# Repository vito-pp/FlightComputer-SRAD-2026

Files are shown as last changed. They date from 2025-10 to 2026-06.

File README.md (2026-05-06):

# FlightComputer-SRAD-2026

---

# RP2040 Firmware Build Instructions

This project uses the Raspberry Pi Pico SDK with CMake and the ARM GCC toolchain.

Follow these steps to set up the build environment.

---

## 1. Install dependencies (Linux)

On Debian/Ubuntu:

```bash
sudo apt update
sudo apt install cmake gcc-arm-none-eabi libnewlib-arm-none-eabi build-essential git
```

On Fedora:

```bash
sudo dnf install cmake arm-none-eabi-gcc-cs arm-none-eabi-newlib make git
```

Check installation:

```bash
arm-none-eabi-gcc --version
cmake --version
```

---

## 2. Download the Pico SDK

Clone the SDK somewhere on your system (outside this repo):

```bash
git clone https://github.com/raspberrypi/pico-sdk.git ~/pico-sdk
```

---

## 3. Set the SDK path environment variable

Set this variable so CMake can find the SDK:

```bash
export PICO_SDK_PATH=~/pico-sdk
```

To make it permanent (bash):

```bash
echo 'export PICO_SDK_PATH=~/pico-sdk' >> ~/.bashrc
source ~/.bashrc
```

---

## 4. Build the project

From the `code/` directory:

```bash
mkdir build
cd build
cmake ..
make -j$(nproc)
```

After building, the firmware file will be generated:

```bash
flight_computer.uf2
```

---

## 5. Flash to the RP2040

1. Hold the **BOOTSEL** button on the Pico
2. Plug the Pico into USB
3. Release BOOTSEL
4. Copy the UF2 file:

```bash
cp flight_computer.uf2 /media/$USER/RPI-RP2/
```

(The mount path may vary depending on your system.)

---

## 6. Rebuilding later

After the first build, you usually only need:

```bash
cd code/build
make -j$(nproc)
```

If you change `CMakeLists.txt`, run:

```bash
cmake ..
```

If something breaks, clean build:

```bash
cd code
rm -rf build
mkdir build
cd build
cmake ..
make -j$(nproc)
```

## Submodules / External Libraries

This project uses the SD-card library `no-OS-FatFS-SD-SDIO-SPI-RPi-Pico` as a Git submodule.

### Fresh clone

Clone with submodules:

```bash
git clone --recurse-submodules <repo-url>
```

### Existing clone

If the repository was already cloned without submodules:

```bash
git submodule update --init --recursive
```

After pulling updates:

```bash
git pull --recurse-submodules
git submodule update --init --recursive
```

### SD-card library notes

This project uses:

```text
no-OS-FatFS-SD-SDIO-SPI-RPi-Pico
```

in SDIO/PIO 4-bit mode.

The library contains a project-specific patch because the SD clock pin is routed differently on this board.

SD pin mapping:

```text
SD_CMD  -> GPIO18
SD_DAT0 -> GPIO19
SD_DAT1 -> GPIO20
SD_DAT2 -> GPIO21
SD_DAT3 -> GPIO22
SD_CLK  -> GPIO25
```

The SDIO PIO configuration was modified with:

```text
SDIO_CLK_PIN_D0_OFFSET = 6
```

The patched submodule commit must be available from the configured submodule remote.

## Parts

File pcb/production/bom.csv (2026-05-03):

Designator | Footprint | Quantity | Value | LCSC Part #
A1 | XDCR_MS561101BA03-50 | 1 | MS561101BA03-50
AE1 | XDCR_W3011 | 1 | W3011
C10, C8 | 0402 | 2 | 1u
C11, C12, C13, C14, C15, C16, C6, C7, C9, CADXL_1, CBAR_1, CBAR_2, CFLASH_1, CIIM_1, CIIM_2, CIIM_3, CIIM_4 | 0402 | 17 | 100n
CADXL_2, CGPS_1, CXB_2 | 0805 | 3 | 1u
CGPS_2 | 0603 | 1 | 100n
CPS_1, CPS_2, CPS_3 | 0805 | 3 | 10u
CXB_1 | 0805 | 1 | 47p
CX_1, CX_2 | 0805 | 2 | 15p
D1 | 0603 | 1 | LED_B
D2 | 0603 | 1 | LED_R
DIV_RES_REG1A1, DIV_RES_REG2A1 | 0805 | 2 | 82k
DIV_RES_REG1B1 | 0805 | 1 | 150k
DIV_RES_REG2B1 | 0805 | 1 | 47k
J1 | MOLEX_503398-1892 | 1 | 503398-1892
J2 | PinHeader_1x03_P2.54mm_Vertical | 1 | Connector_3
J3 | USB_Micro-B_Amphenol_10103594-0001LF_Horizontal | 1 | USB_B_Micro
J5 | Molex_1x02_P2.54mm | 1 | Vin_Bat
LS1 | Buzzer_TDK_PS1240P02BT_D12.2mm_H6.5mm | 1 | PS1240P02BT
Q1 | SOT-23 | 1 | BC847
R1 | 0805 | 1 | 22k
R2, RFLASH_2, RX_1 | 0805 | 3 | 1k
R3, R4 | 0603 | 2 | 27
R6, R7, R_RST1 | 0805 | 3 | 10k
RI2C_1, RI2C_2, RI2C_3, RI2C_4 | 0603 | 4 | 1k
RL_1 | 0805 | 1 | 39
RL_2 | 0805 | 1 | 150
RSPI_4 | 0603 | 1 | 10k
S1, S2 | PTS810SJK250SMTRLFS | 2 | PTS810SJK250SMTR_LFS
TP1, TP2, TP3 | TestPoint_Pad_D1.0mm | 3 | TestPoint
U1 | QFN50P450X450X115-25N | 1 | IIM-20670
U3 | QFN-56-1EP_7x7mm_P0.4mm_EP3.2x3.2mm_ThermalVias | 1 | RP2040
U4 | LGA-14_3x5mm_P0.8mm_LayoutBorder1x6y | 1 | ADXL375BCCZ-RL7
U5 | XCVR_MAX-M10M-00B | 1 | MAX-M10M-00B
U6 | SOIC-8_5.3x5.3mm_P1.27mm | 1 | W25Q128JVS
U7 | XBEEPRO | 1 | XBP9B-DMSTB002
U8 | SOT-223-6 | 1 | TPS73733DCQ
Y1 | XTAL_ABM8-272-T3 | 1 | ABM8-272-T3

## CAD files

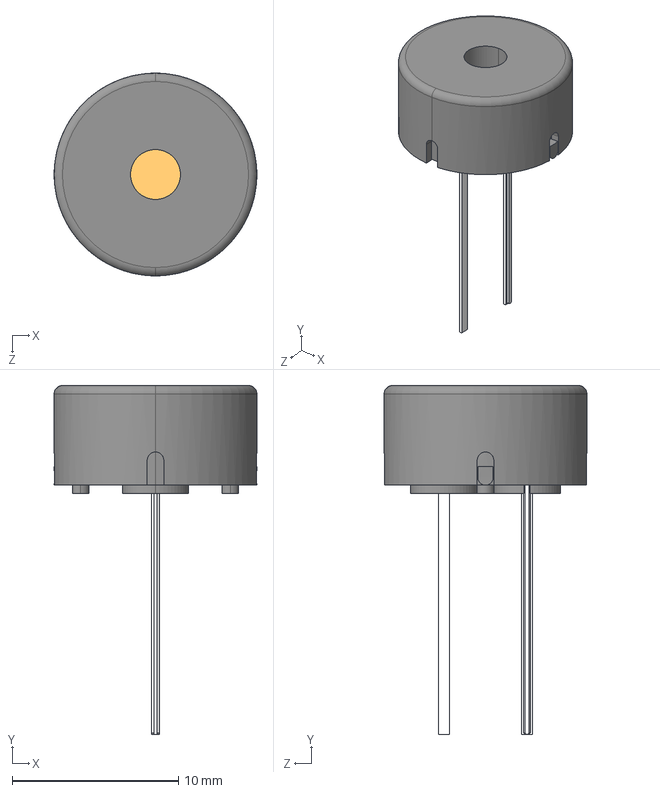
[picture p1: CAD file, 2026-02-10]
pcb/components/3d_models/PS1240P02BT.step
12.2 x 21.0 x 12.2 mm

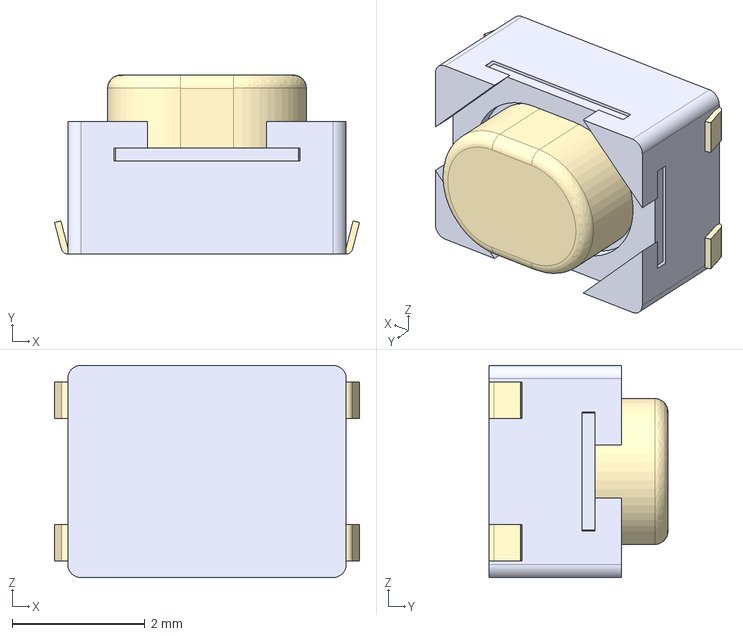
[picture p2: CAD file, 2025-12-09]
pcb/components/3d_models/PTS810SJK250SMTR_LFS.step
4.60 x 2.70 x 3.20 mm

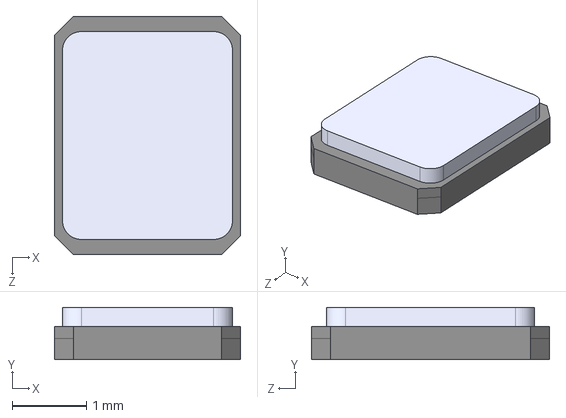
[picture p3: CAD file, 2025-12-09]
pcb/components/3d_models/ABM8-272-T3.STEP
2.50 x 0.7 x 3.20 mm

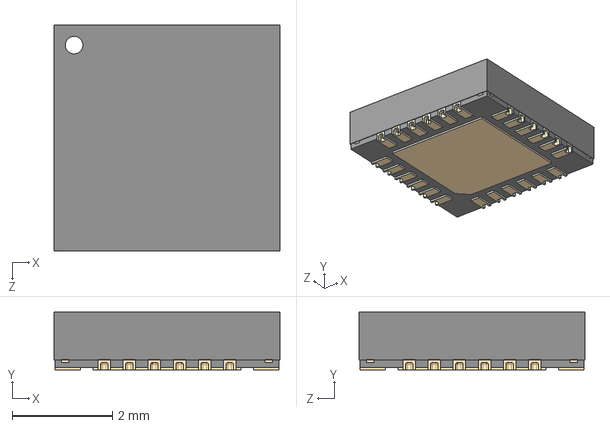
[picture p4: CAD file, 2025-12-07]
pcb/components/3d_models/IIM-20670--3DModel-STEP-269445.STEP
4.50 x 1.15 x 4.50 mm

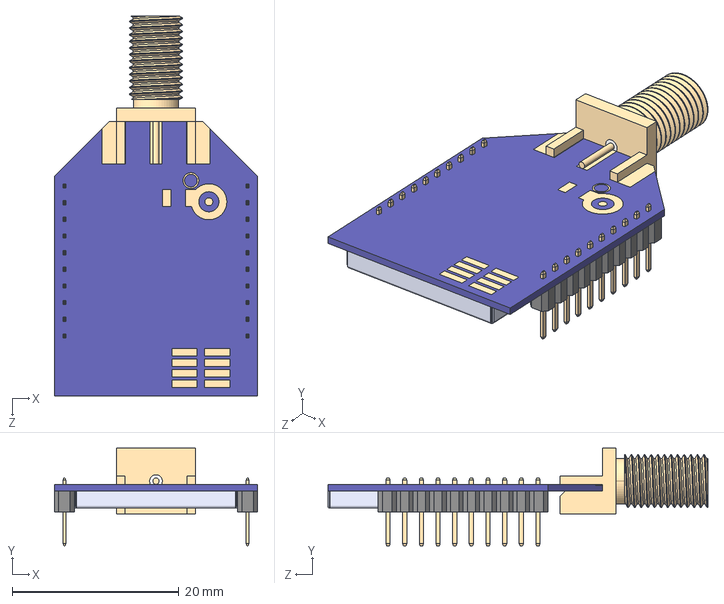
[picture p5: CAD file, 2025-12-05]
pcb/components/3d_models/XBP9B-DMSTB002.step
24.4 x 11.7 x 45.6 mm

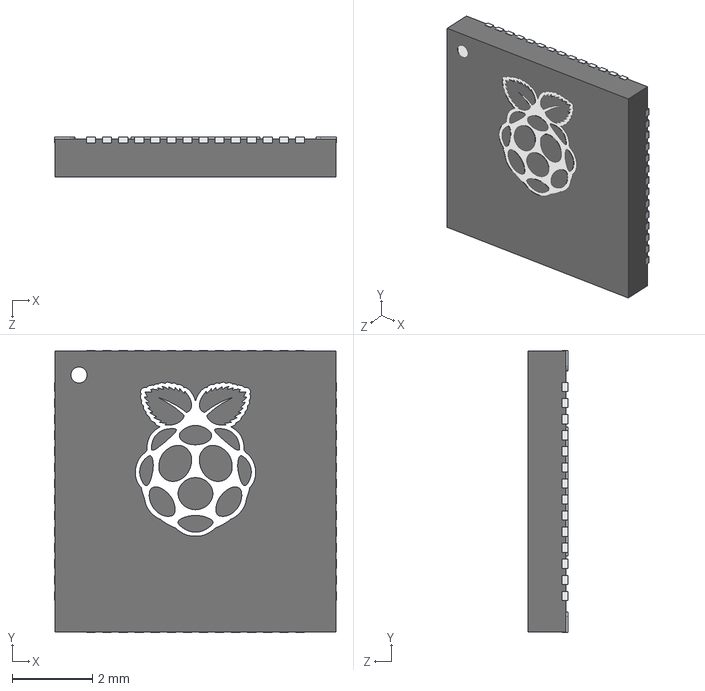
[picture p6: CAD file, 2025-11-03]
pcb/components/3d_models/RP2040_QFN_PACKAGE.STEP
7.02 x 7.02 x 1.00 mm

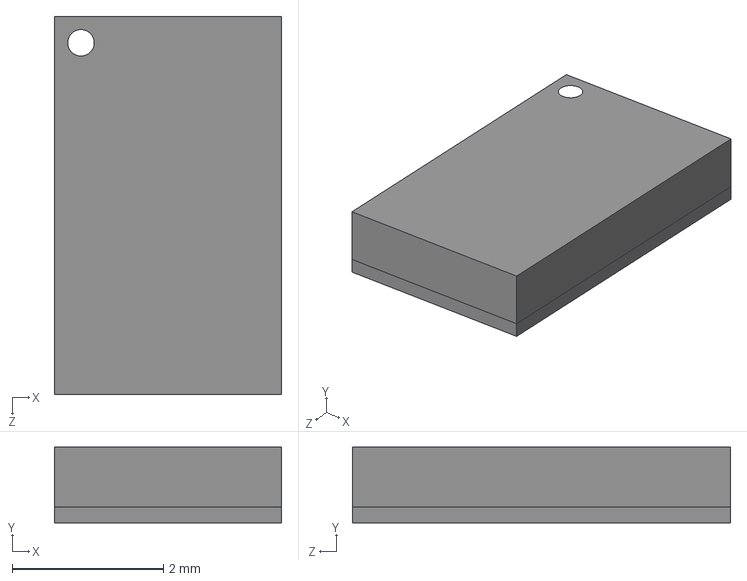
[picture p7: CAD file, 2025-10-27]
pcb/components/3d_models/ADXL375BCCZ-RL7.STEP
3.00 x 1.00 x 5.00 mm

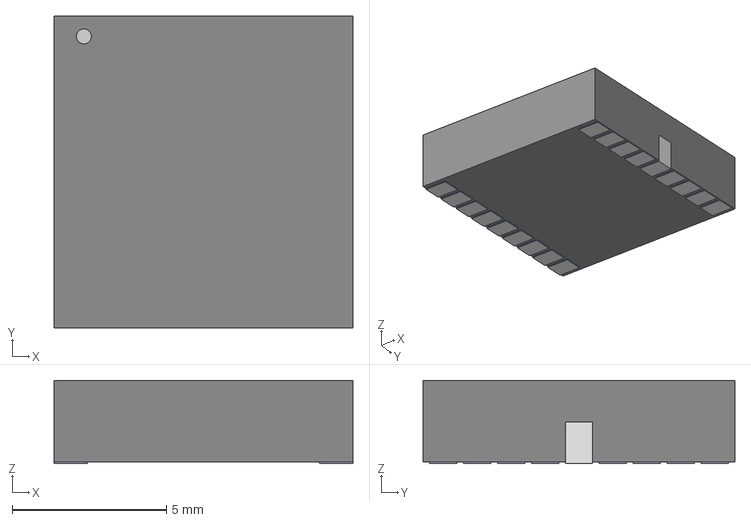
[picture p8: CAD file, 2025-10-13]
pcb/components/3d_models/MOD18_MAX-M10M_UBL.step
9.70 x 10.1 x 2.69 mm

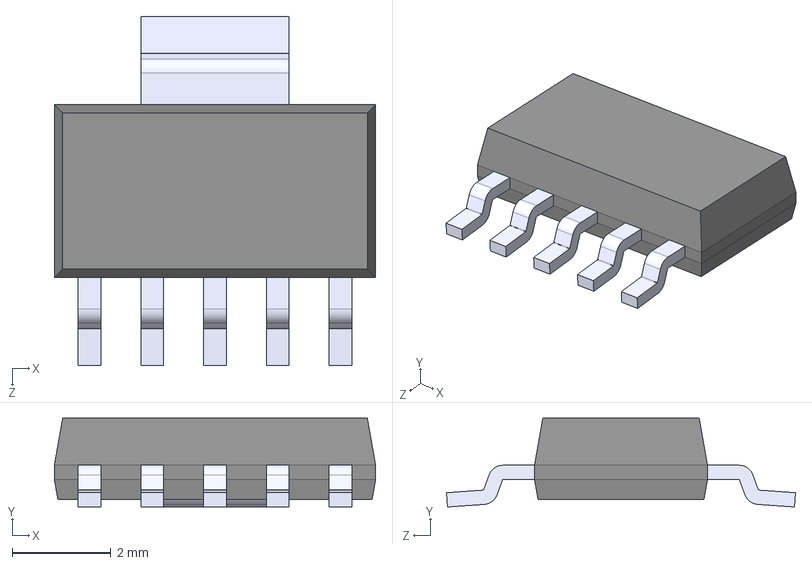
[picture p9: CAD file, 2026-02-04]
pcb/components/symbols/TPS73733DCQ.step
6.50 x 1.80 x 7.06 mm

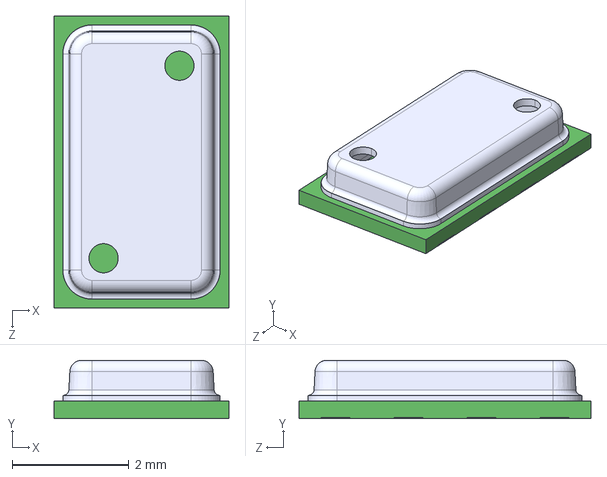
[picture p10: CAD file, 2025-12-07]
pcb/components/3d_models/MS561101BA03-50--3DModel-STEP-56544.STEP
3.00 x 1.00 x 5.00 mm

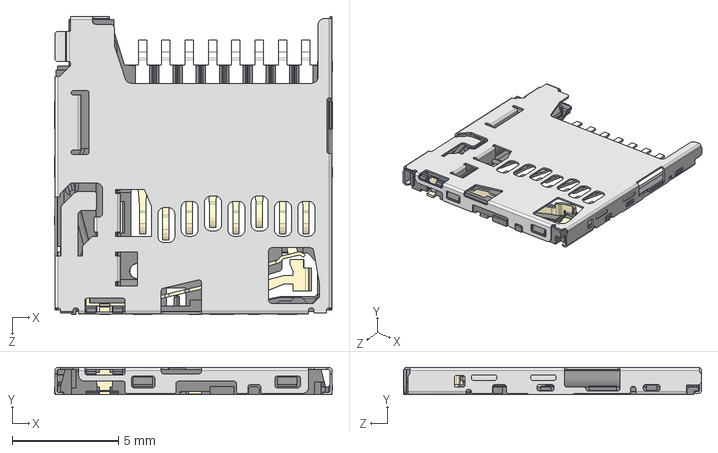
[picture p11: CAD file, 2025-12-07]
pcb/components/3d_models/503398-1892--3DModel-STEP-56544.STEP
13.1 x 1.28 x 14.1 mm

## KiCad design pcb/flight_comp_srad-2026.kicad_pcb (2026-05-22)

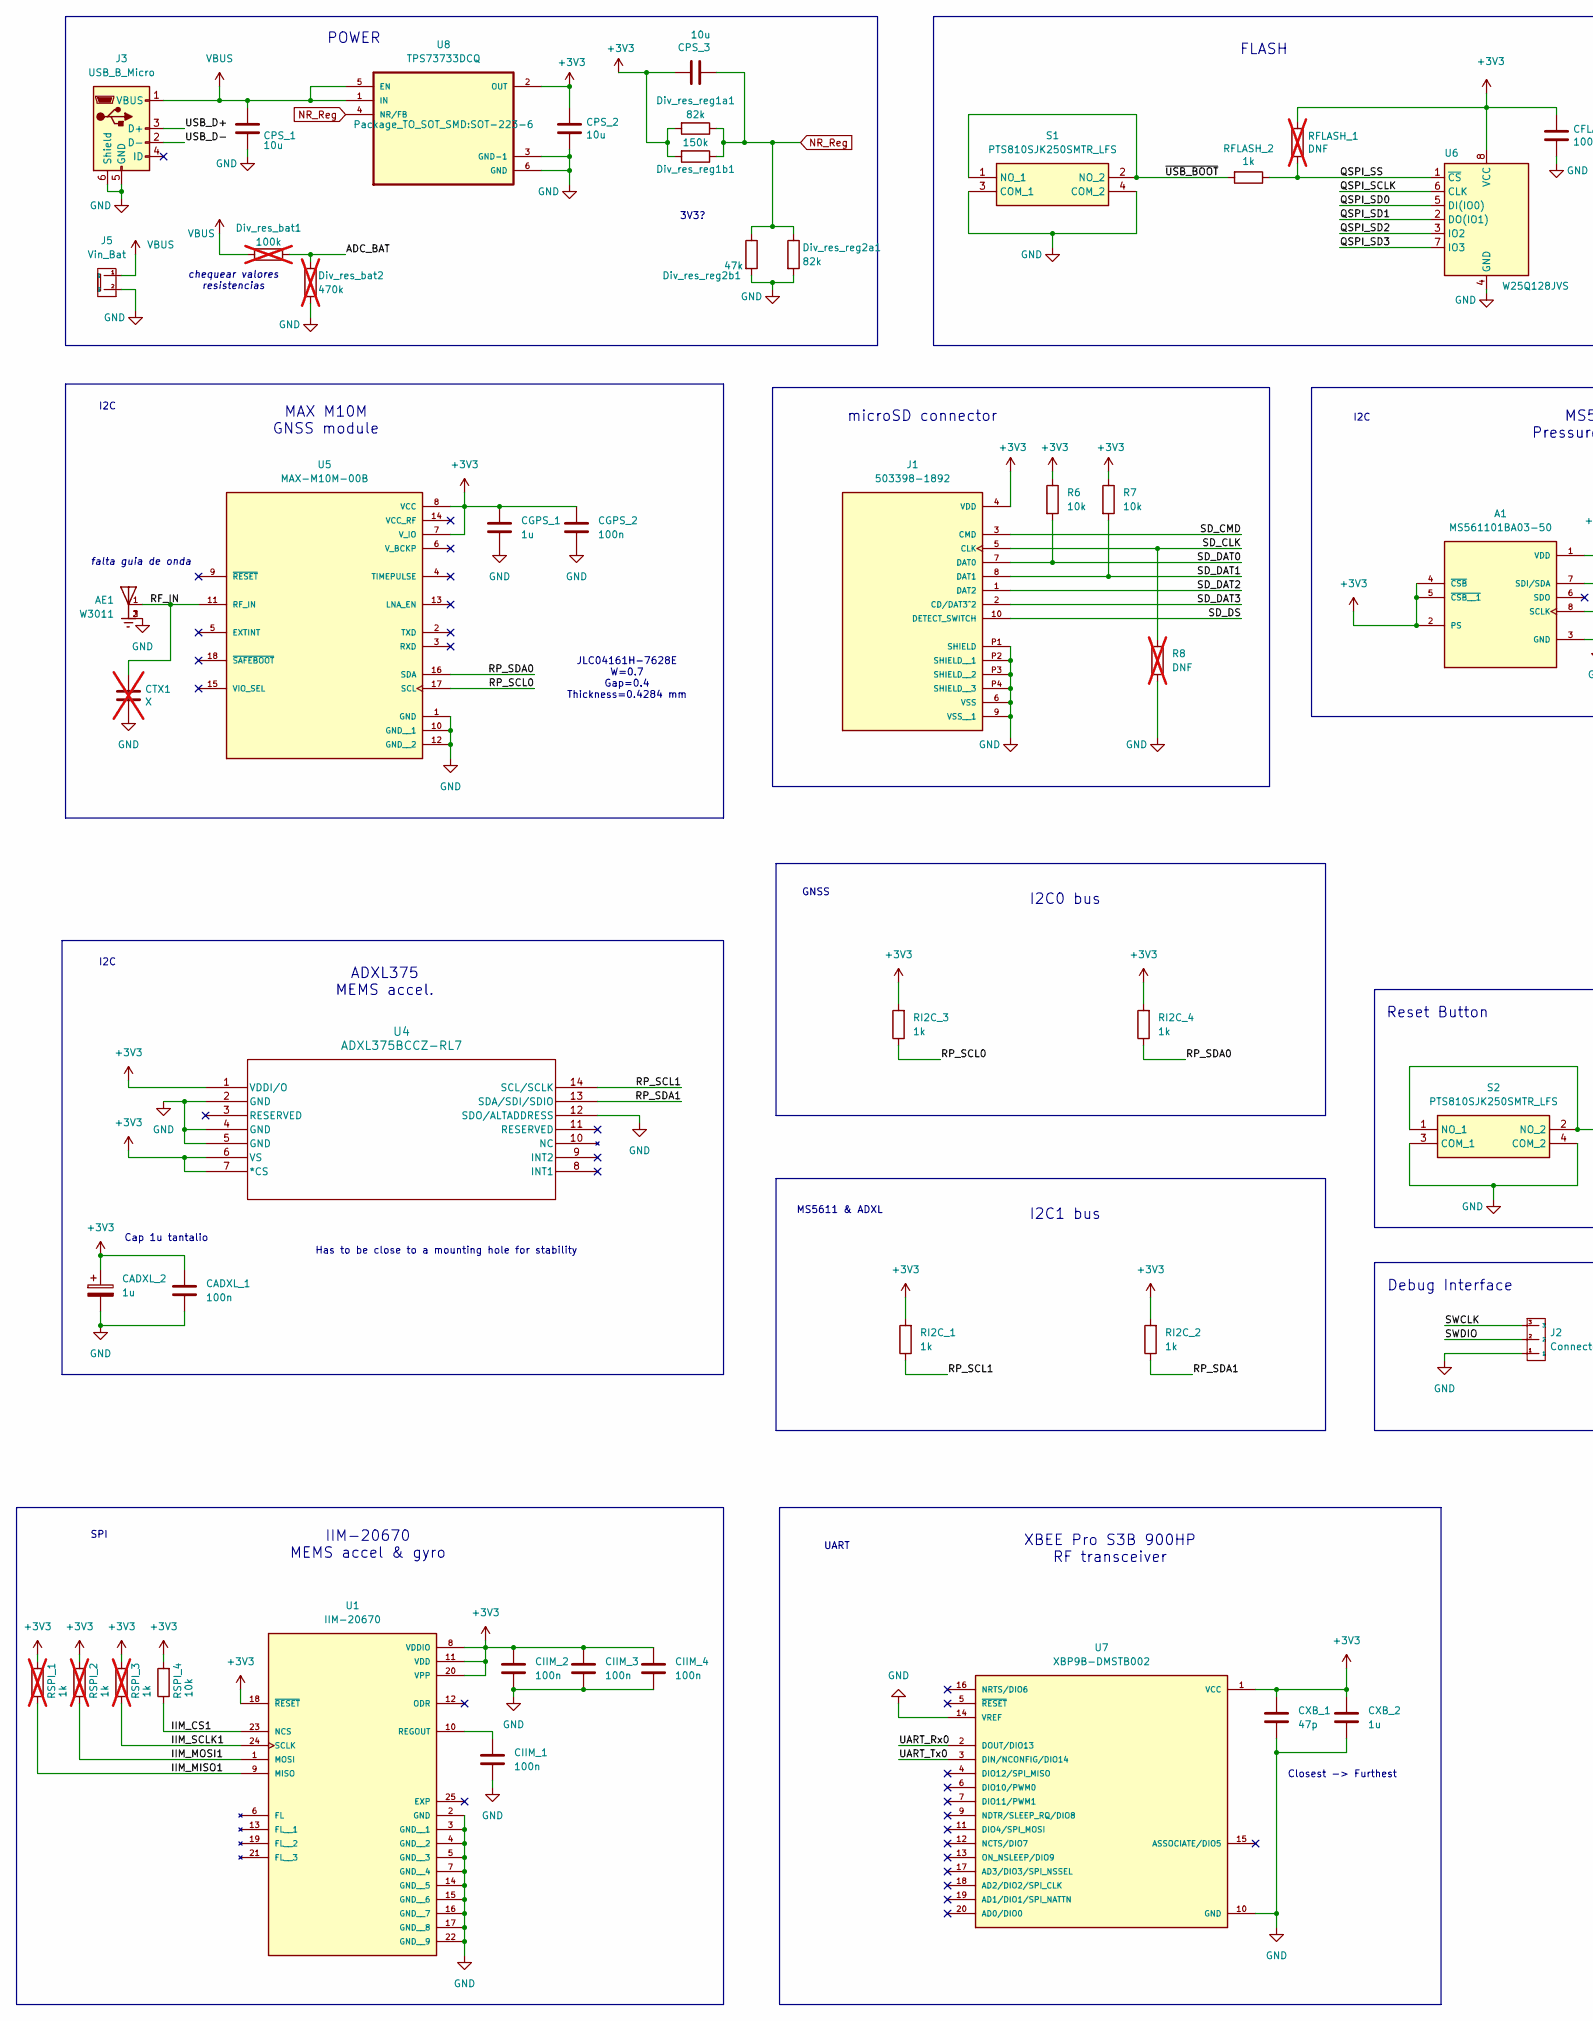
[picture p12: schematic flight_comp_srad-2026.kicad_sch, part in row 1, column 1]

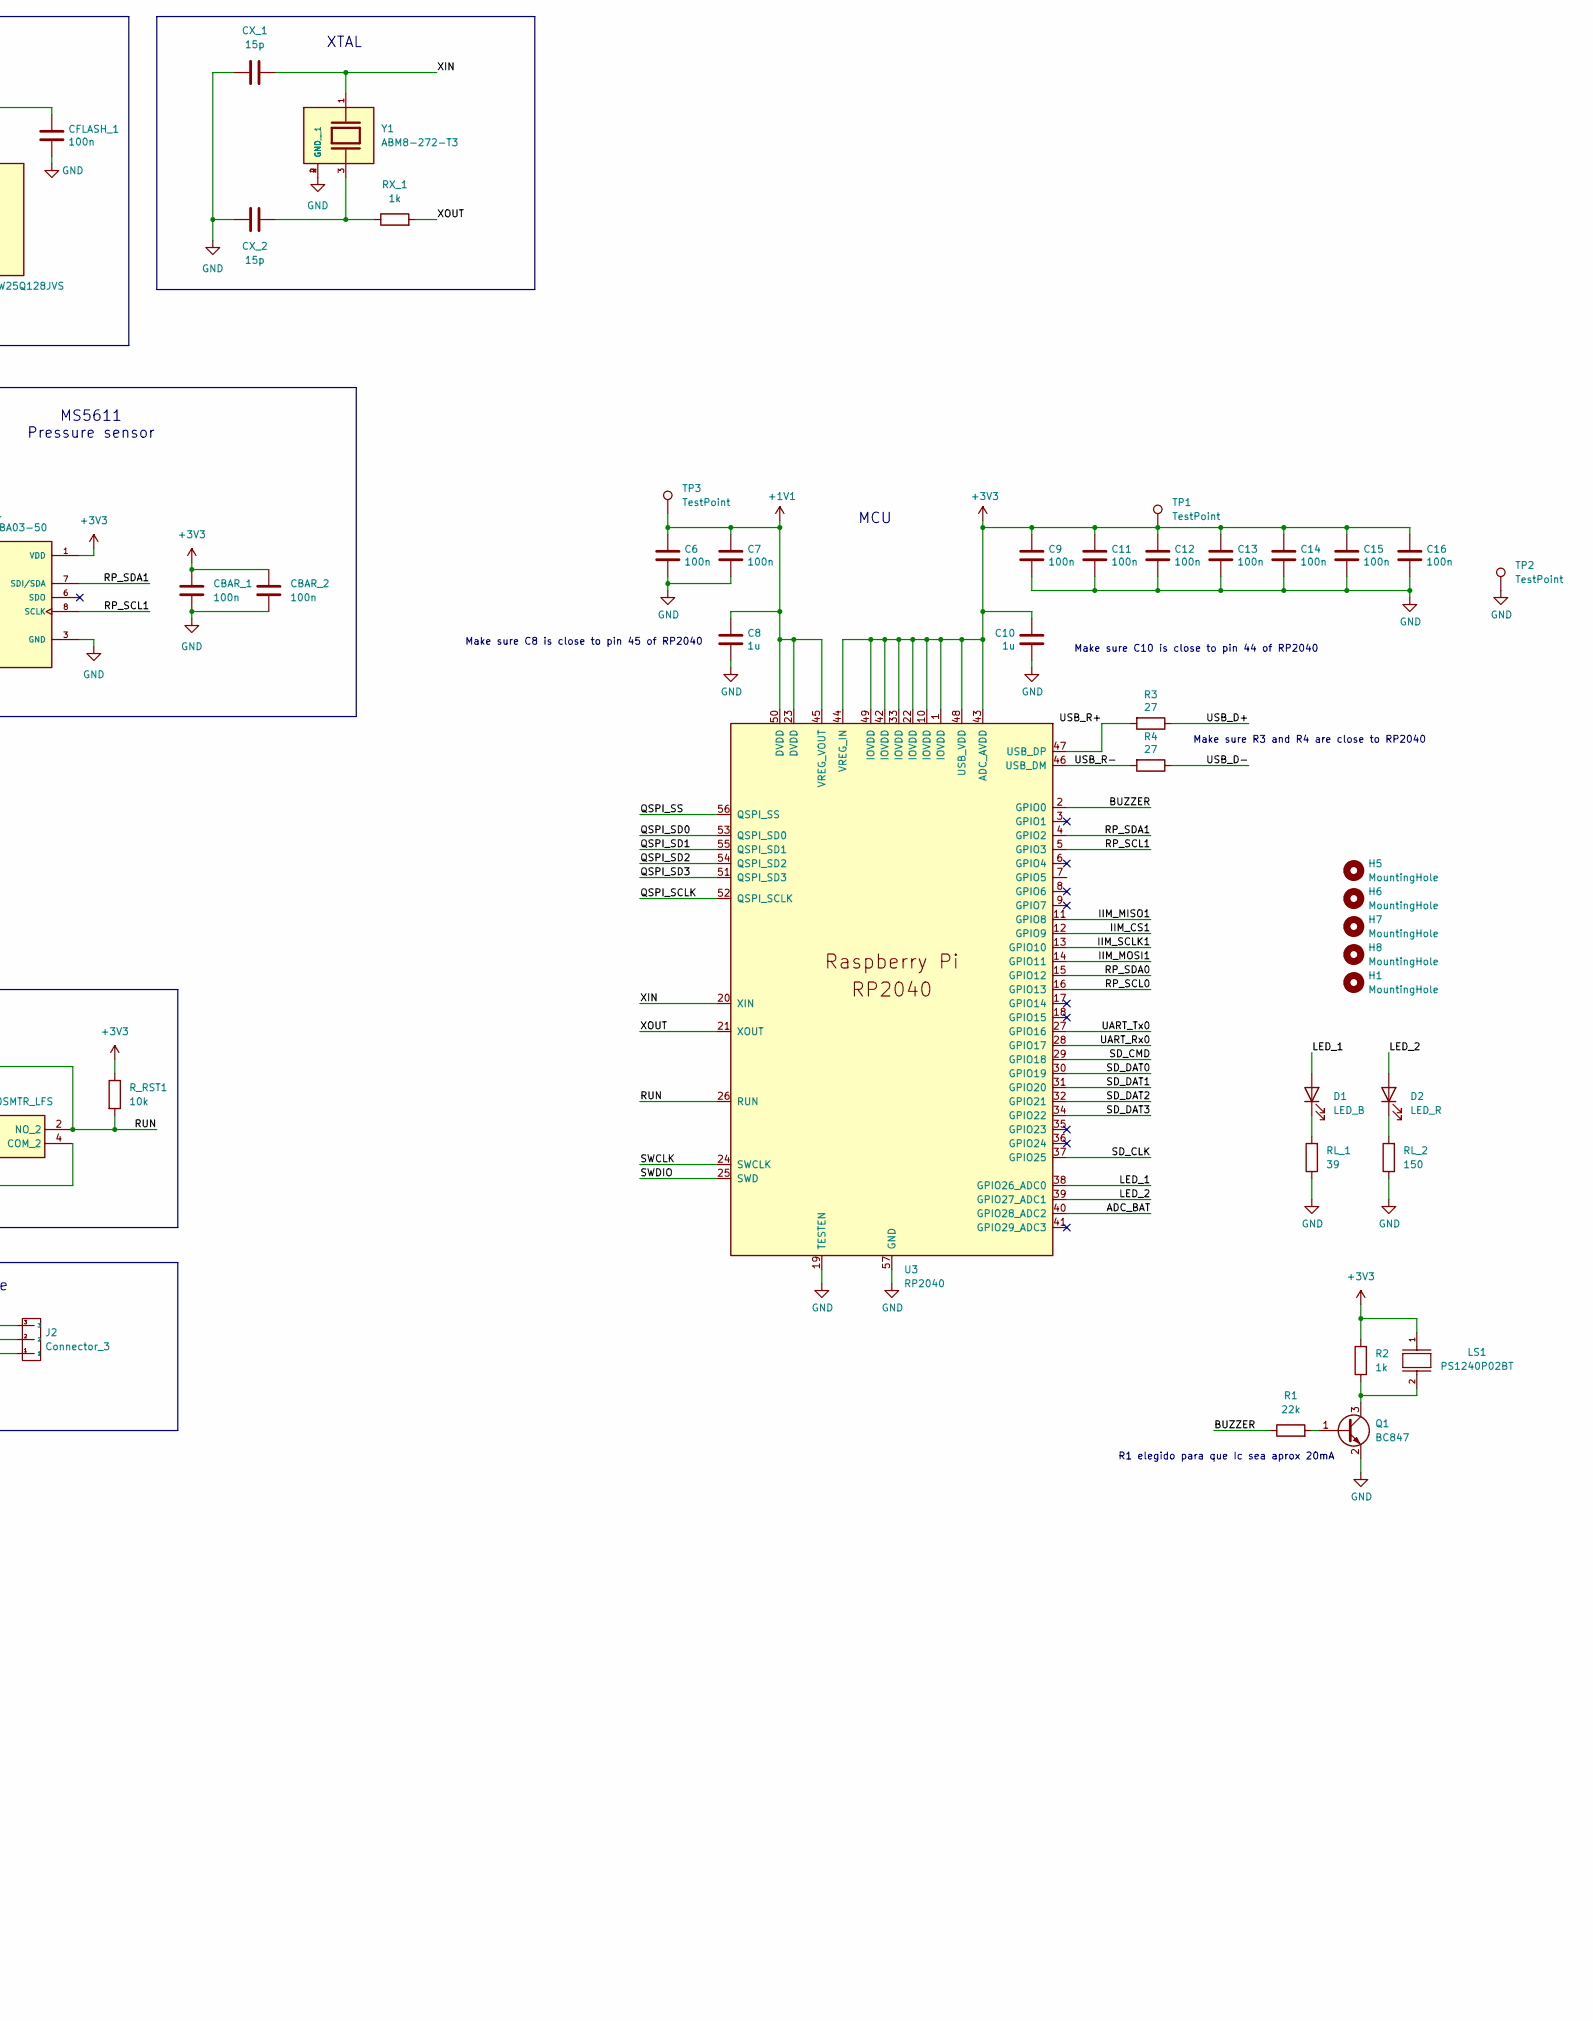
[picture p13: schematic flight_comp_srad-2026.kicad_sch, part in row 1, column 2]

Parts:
A1: MS561101BA03-50; XDCR_MS561101BA03-50; PARTREV 06/2017
AE1: W3011; XDCR_W3011; PARTREV N/A
C6, C7, C9, C11, C12, C13, C14, C15, C16: 100n; C_0402_1005Metric
C8, C10: 1u; C_0402_1005Metric
CADXL_1: 100n; C_0402_1005Metric
CADXL_2: 1u; C_0805_2012Metric
CBAR_1, CBAR_2: 100n; C_0402_1005Metric
CFLASH_1: 100n; C_0402_1005Metric
CGPS_1: 1u; C_0805_2012Metric
CGPS_2: 100n; C_0603_1608Metric
CIIM_1, CIIM_2, CIIM_3, CIIM_4: 100n; C_0402_1005Metric
CPS_1, CPS_2, CPS_3: 10u; C_0805_2012Metric
CTX1: X; C_0805_2012Metric; not fitted
CXB_1: 47p; C_0805_2012Metric
CXB_2: 1u; C_0805_2012Metric
CX_1, CX_2: 15p; C_0805_2012Metric
D1: LED_B; LED_0603_1608Metric
D2: LED_R; LED_0603_1608Metric
Div_res_bat1: 100k; R_0805_2012Metric; not fitted
Div_res_bat2: 470k; R_0805_2012Metric; not fitted
Div_res_reg1a1, Div_res_reg2a1: 82k; R_0805_2012Metric
Div_res_reg1b1: 150k; R_0805_2012Metric
Div_res_reg2b1: 47k; R_0805_2012Metric
H1, H5, H6, H7, H8: MountingHole; MountingHole_3mm
J1: 503398-1892; MOLEX_503398-1892; PARTREV 0
J2: Connector_3; PinHeader_1x03_P2.54mm_Vertical
J3: USB_B_Micro; USB_Micro-B_Amphenol_10103594-0001LF_Horizontal
J5: Vin_Bat; Molex_1x02_P2.54mm
LS1: PS1240P02BT; Buzzer_TDK_PS1240P02BT_D12.2mm_H6.5mm
Q1: BC847; SOT-23
R1: 22k; R_0805_2012Metric
R2: 1k; R_0805_2012Metric
R3, R4: 27; R_0603_1608Metric
R6, R7: 10k; R_0805_2012Metric
R8: DNF; R_0805_2012Metric; not fitted
RFLASH_1: DNF; R_0805_2012Metric; not fitted
RFLASH_2: 1k; R_0805_2012Metric
RI2C_1, RI2C_2, RI2C_3, RI2C_4: 1k; R_0603_1608Metric
RL_1: 39; R_0805_2012Metric
RL_2: 150; R_0805_2012Metric
RSPI_1, RSPI_2, RSPI_3: 1k; R_0603_1608Metric; not fitted
RSPI_4: 10k; R_0603_1608Metric
RX_1: 1k; R_0805_2012Metric
R_RST1: 10k; R_0805_2012Metric
S1, S2: PTS810SJK250SMTR_LFS; PTS810SJK250SMTRLFS; Mouser Part Number 611-PTS810SJK250SMTR
TP1, TP2, TP3: TestPoint; TestPoint_Pad_D1.0mm
U1: IIM-20670; QFN50P450X450X115-25N; PARTREV 1.1
U3: RP2040; QFN-56-1EP_7x7mm_P0.4mm_EP3.2x3.2mm_ThermalVias
U4: ADXL375BCCZ-RL7; LGA-14_3x5mm_P0.8mm_LayoutBorder1x6y
U5: MAX-M10M-00B; XCVR_MAX-M10M-00B; PARTREV C1
U6: W25Q128JVS; SOIC-8_5.3x5.3mm_P1.27mm
U7: XBP9B-DMSTB002; XBEEPRO
U8: TPS73733DCQ; SOT-223-6
Y1: ABM8-272-T3; XTAL_ABM8-272-T3; PARTREV 07-29-20

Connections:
+1V1: C6.1, C7.1, C8.1, TP3.1, U3.23 (DVDD), U3.45 (VREG_VOUT), U3.50 (DVDD)
+3V3: A1.1 (VDD), A1.2 (PS), A1.4 (~CSB), A1.5 (~CSB__1), C9.1, C10.1, C11.1, C12.1, C13.1, C14.1, C15.1, C16.1, CADXL_1.1, CADXL_2.1, CBAR_1.1, CBAR_2.1, CFLASH_1.1, CGPS_1.1, CGPS_2.1, CIIM_2.1, CIIM_3.1, CIIM_4.1, CPS_2.1, CPS_3.1, CXB_1.1, CXB_2.1, Div_res_reg1a1.2, Div_res_reg1b1.2, J1.4 (VDD), LS1.1, R2.2, R6.1, R7.1, RFLASH_1.1, RI2C_1.2, RI2C_2.2, RI2C_3.2, RI2C_4.2, RSPI_1.2, RSPI_2.2, RSPI_3.2, RSPI_4.2, R_RST1.1, TP1.1, U1.8 (VDDIO), U1.11 (VDD), U1.18 (~RESET), U1.20 (VPP), U3.1 (IOVDD), U3.10 (IOVDD), U3.22 (IOVDD), U3.33 (IOVDD), U3.42 (IOVDD), U3.43 (ADC_AVDD), U3.44 (VREG_IN), U3.48 (USB_VDD), U3.49 (IOVDD), U4.1 (VDDI/O), U4.6 (VS), U4.7 (*CS), U5.7 (V_IO), U5.8 (VCC), U6.8 (VCC), U7.1 (VCC), U8.2 (OUT)
/ADC_BAT: Div_res_bat1.1, Div_res_bat2.1, U3.40 (GPIO28_ADC2)
/BUZZER: R1.1, U3.2 (GPIO0)
/IIM_CS1: RSPI_4.1, U1.23 (NCS), U3.12 (GPIO9)
/IIM_MISO1: RSPI_1.1, U1.9 (MISO), U3.11 (GPIO8)
/IIM_MOSI1: RSPI_2.1, U1.1 (MOSI), U3.14 (GPIO11)
/IIM_SCLK1: RSPI_3.1, U1.24 (SCLK), U3.13 (GPIO10)
/LED_1: D1.2 (A), U3.38 (GPIO26_ADC0)
/LED_2: D2.2 (A), U3.39 (GPIO27_ADC1)
/QSPI_SCLK: U3.52 (QSPI_SCLK), U6.6 (CLK)
/QSPI_SD0: U3.53 (QSPI_SD0), U6.5 (DI(IO0))
/QSPI_SD1: U3.55 (QSPI_SD1), U6.2 (DO(IO1))
/QSPI_SD2: U3.54 (QSPI_SD2), U6.3 (IO2)
/QSPI_SD3: U3.51 (QSPI_SD3), U6.7 (IO3)
/QSPI_SS: RFLASH_1.2, RFLASH_2.1, U3.56 (QSPI_SS), U6.1 (~CS)
/RF_IN: AE1.1, CTX1.1, U5.11 (RF_IN)
/RP_SCL0: RI2C_3.1, U3.16 (GPIO13), U5.17 (SCL)
/RP_SCL1: A1.8 (SCLK), RI2C_1.1, U3.5 (GPIO3), U4.14 (SCL/SCLK)
/RP_SDA0: RI2C_4.1, U3.15 (GPIO12), U5.16 (SDA)
/RP_SDA1: A1.7 (SDI/SDA), RI2C_2.1, U3.4 (GPIO2), U4.13 (SDA/SDI/SDIO)
/RUN: R_RST1.2, S2.1 (NO_1), S2.2 (NO_2), U3.26 (RUN)
/SD_CLK: J1.5 (CLK), R8.1, U3.37 (GPIO25)
/SD_CMD: J1.3 (CMD), U3.29 (GPIO18)
/SD_DAT0: J1.7 (DAT0), R6.2, U3.30 (GPIO19)
/SD_DAT1: J1.8 (DAT1), R7.2, U3.31 (GPIO20)
/SD_DAT2: J1.1 (DAT2), U3.32 (GPIO21)
/SD_DAT3: J1.2 (CD/DAT3^2), U3.34 (GPIO22)
/SD_DS: J1.10 (DETECT_SWITCH)
/SWCLK: J2.3, U3.24 (SWCLK)
/SWDIO: J2.2, U3.25 (SWD)
/UART_Rx0: U3.28 (GPIO17), U7.2 (DOUT/DIO13)
/UART_Tx0: U3.27 (GPIO16), U7.3 (DIN/NCONFIG/DIO14)
/USB_D+: J3.3 (D+), R3.1
/USB_D-: J3.2 (D-), R4.1
/USB_R+: R3.2, U3.47 (USB_DP)
/USB_R-: R4.2, U3.46 (USB_DM)
/XIN: CX_1.2, U3.20 (XIN), Y1.1
/XOUT: RX_1.2, U3.21 (XOUT)
/~USB_BOOT: RFLASH_2.2, S1.1 (NO_1), S1.2 (NO_2)
GND: A1.3 (GND), AE1.2, AE1.3, C6.2, C7.2, C8.2, C9.2, C10.2, C11.2, C12.2, C13.2, C14.2, C15.2, C16.2, CADXL_1.2, CADXL_2.2, CBAR_1.2, CBAR_2.2, CFLASH_1.2, CGPS_1.2, CGPS_2.2, CIIM_1.2, CIIM_2.2, CIIM_3.2, CIIM_4.2, CPS_1.2, CPS_2.2, CTX1.2, CXB_1.2, CXB_2.2, CX_1.1, CX_2.1, Div_res_bat2.2, Div_res_reg2a1.2, Div_res_reg2b1.2, J1.6 (VSS), J1.9 (VSS__1), J1.P1 (SHIELD), J1.P2 (SHIELD__1), J1.P3 (SHIELD__2), J1.P4 (SHIELD__3), J2.1, J3.5 (GND), J3.6 (Shield), J5.2, Q1.2 (E), R8.2, RL_1.1, RL_2.1, S1.3 (COM_1), S1.4 (COM_2), S2.3 (COM_1), S2.4 (COM_2), TP2.1, U1.2 (GND), U1.3 (GND__1), U1.4 (GND__2), U1.5 (GND__3), U1.7 (GND__4), U1.14 (GND__5), U1.15 (GND__6), U1.16 (GND__7), U1.17 (GND__8), U1.22 (GND__9), U3.19 (TESTEN), U3.57 (GND), U4.2 (GND), U4.4 (GND), U4.5 (GND), U4.12 (SDO/ALTADDRESS), U5.1 (GND), U5.10 (GND__1), U5.12 (GND__2), U6.4 (GND), U7.10 (GND), U7.14 (VREF), U8.3 (GND-1), U8.6 (GND), Y1.2 (GND), Y1.4 (GND__1)
NR_Reg: CPS_3.2, Div_res_reg1a1.1, Div_res_reg1b1.1, Div_res_reg2a1.1, Div_res_reg2b1.1, U8.4 (NR/FB)
unnamed: CX_2.2, RX_1.1, Y1.3
unnamed: D1.1 (K), RL_1.2
unnamed: D2.1 (K), RL_2.2
unnamed: Q1.1 (B), R1.2
unnamed: LS1.2, Q1.3 (C), R2.1
unnamed: CIIM_1.1, U1.10 (REGOUT)
VBUS: CPS_1.1, Div_res_bat1.2, J3.1 (VBUS), J5.1, U8.1 (IN), U8.5 (EN)

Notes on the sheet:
ADXL375 MEMS accel.
microSD connector
MAX M10M GNSS module
Make sure C8 is close to pin 45 of RP2040
MS5611 Pressure sensor
I2C
IIM-20670 MEMS accel & gyro
Reset Button
MCU
GNSS
chequear valores resistencias
falta guia de onda
I2C1 bus
Closest -> Furthest
3V3?
JLC04161H-7628E W=0.7 Gap=0.4 Thickness=0.4284 mm
I2C0 bus
SPI
Make sure C10 is close to pin 44 of RP2040
XBEE Pro S3B 900HP RF transceiver
Debug Interface
FLASH
Has to be close to a mounting hole for stability
Cap 1u tantalio
UART
MS5611 & ADXL
Make sure R3 and R4 are close to RP2040
R1 elegido para que Ic sea aprox 20mA
XTAL
POWER

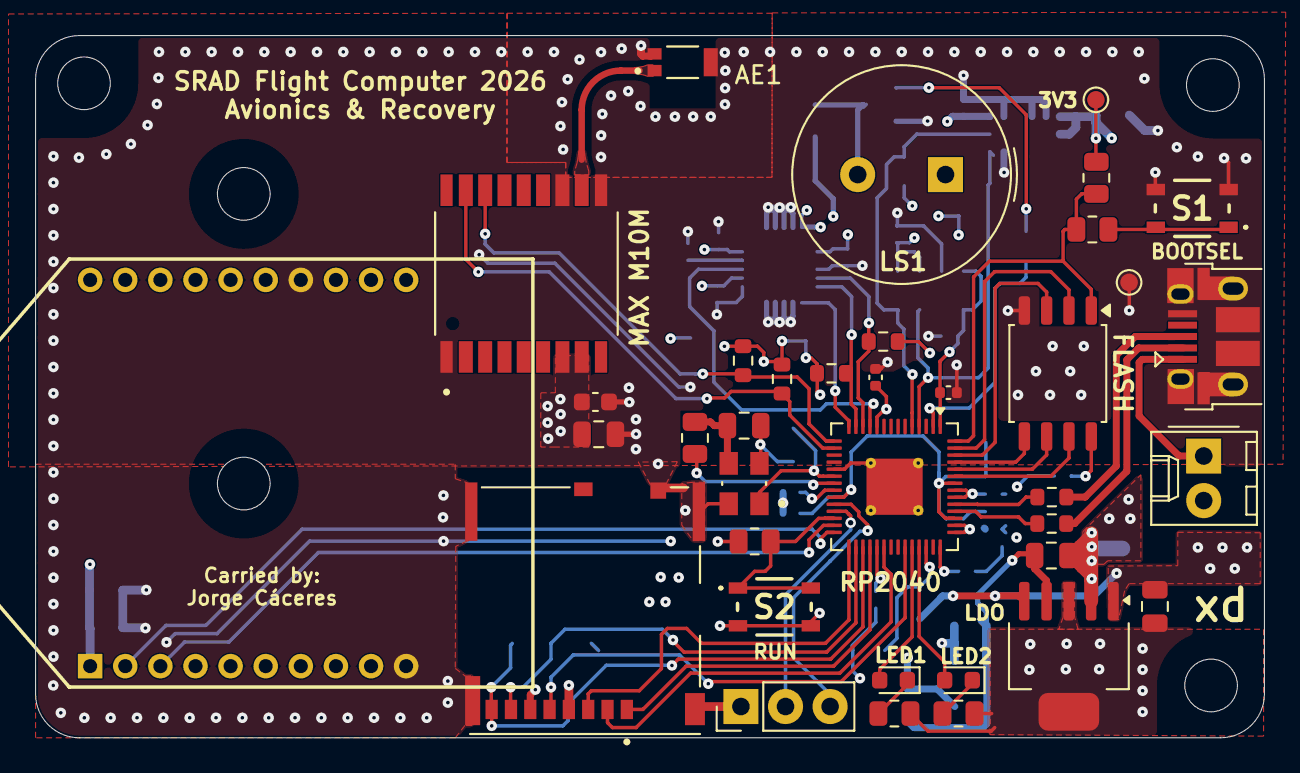
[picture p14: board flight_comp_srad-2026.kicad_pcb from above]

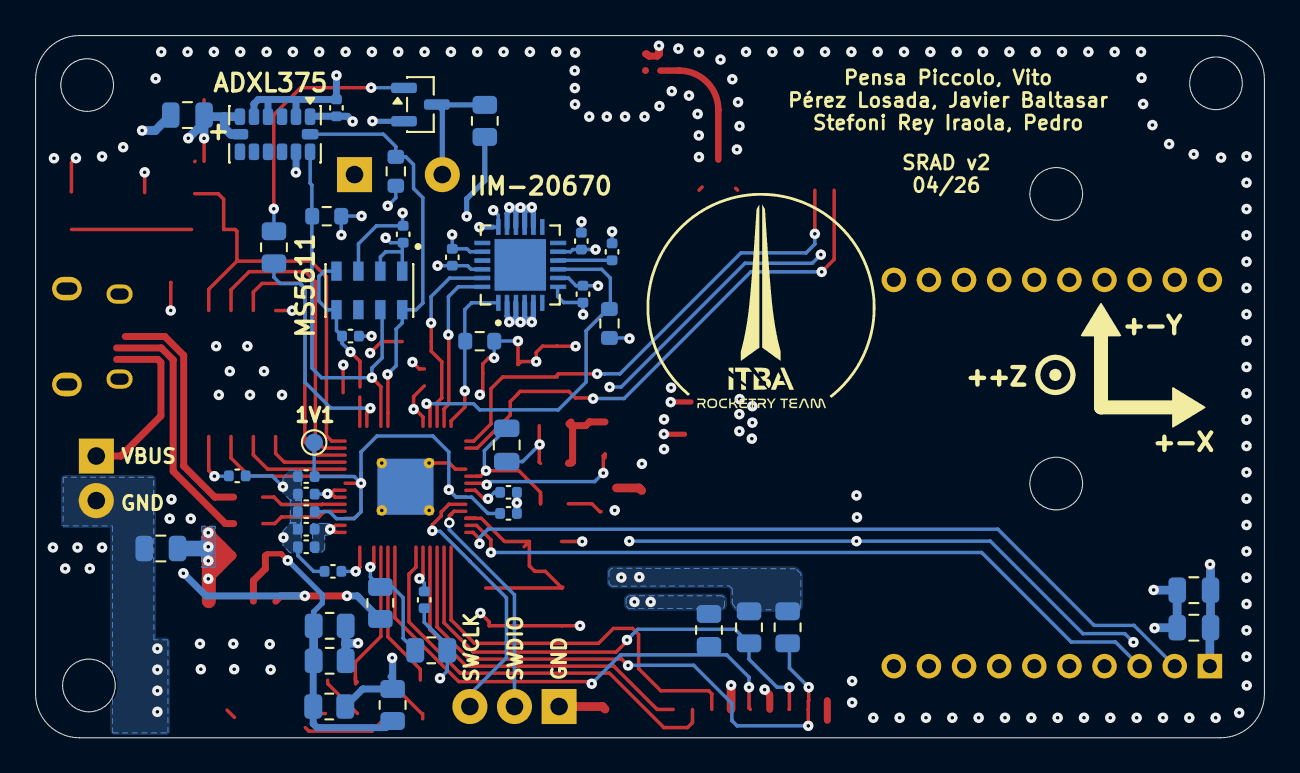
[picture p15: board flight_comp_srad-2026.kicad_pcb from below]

Board: 4 copper layers, 70.0 x 40.0 mm, 84 parts (42 on the bottom side), 48 nets.

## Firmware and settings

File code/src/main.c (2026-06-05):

#include <stdio.h>
#include <stdint.h>
#include <stdbool.h>

#include "pico/stdlib.h"
#include "pico/multicore.h"

#include "drvs/iim20670.h"
#include "drvs/buzzer.h"
#include "drvs/ms5611.h"
#include "drvs/adxl375.h"
#include "drvs/adc_bat_lvl.h"
#include "frame_ring_buffer.h"
#include "drvs/sd_logger.h"
#include "drvs/xbee.h"
#include "app_crc.h"
// #include "drvs/max_m10s.h" // it doesnt work :(

#define EVER (;;) // forever ever, baby...

// GPIOs
#define BLUE_LED 26
#define RED_LED 27

// Masks for freshness bitfield
#define FRAME_IMU_FRESH   (1u << 0)
#define FRAME_ADXL_FRESH  (1u << 1)
#define FRAME_BARO_FRESH  (1u << 2)
#define FRAME_GNSS_FRESH  (1u << 3)

#define FRAME_PERIOD_US 10000 // 100 Hz

void core1_entry(void);
void error_handler(void);
void serial_debug_print(sensor_frame_t *frame);
void log_frame_to_sd(sensor_frame_t *frame);

typedef struct {
	bool fresh;
	iim_sample_t sample;
} latest_imu_t;

typedef struct {
	bool fresh;
	adxl375_sample_t sample;
} latest_adxl_t;

typedef struct {
	bool fresh;
	ms5611_sample_t sample;
} latest_baro_t;

typedef struct {
	bool fresh;
	uint16_t sample_mv;
} latest_battery_t;

// typedef struct {
// 	bool fresh;
// 	gnss_sample_t sample;
// } latest_gnss_t;

// frame ring buffer for all readings and frame counter
static frame_ring_t frame_rb = {0};
static uint32_t frame_number = 0;

int main(void)
{
	buzz_init();
	buzz_alarm(true);

	gpio_init(BLUE_LED);
	gpio_set_dir(BLUE_LED, GPIO_OUT);
	gpio_put(BLUE_LED, 1);

	gpio_init(RED_LED);
	gpio_set_dir(RED_LED, GPIO_OUT);
	gpio_put(RED_LED, 0);

	adc_bat_lvl_init();

	stdio_init_all();
	sleep_ms(2000);

	if (!sd_logger_init()) {
		printf("SD logger init failed\n");
		error_handler();
	}
	printf("SD logger init OK\n");

	xbee_init();
	printf("XBee init OK\n");

	if (!(ms5611_init() && iim_init() && adxl375_init())) {
		printf("Sensors init failed\n");
		error_handler();
	}
	printf("Sensors init OK\n");

	printf("Calibrating barometer, IMU, and ADXL...\n");
	if (!(ms5611_calibrate() && iim_calibrate() && adxl375_calibrate())) {
		printf("Calibration failed\n");
		error_handler();
	}
	printf("Calibration done\n");

	// if (!max_m10s_init()) {
	// 	printf("GNSS init failed\n");
	// 	error_handler();
	// }
	// printf("GNSS init OK\n");

	latest_imu_t latest_imu = {0};
	latest_adxl_t latest_adxl = {0};
	latest_baro_t latest_baro = {0};
	latest_battery_t latest_battery = {0};
	// latest_gnss_t latest_gnss = {0};

	uint64_t next_frame_us = time_us_64();

	multicore_launch_core1(core1_entry);

	sleep_ms(1000);
	buzz_alarm(false);
	gpio_put(BLUE_LED, 0);

	for EVER {
		uint64_t now = time_us_64();

		iim_sample_t imu_tmp;
		if (iim_poll_sample(&imu_tmp) == IIM_POLL_OK) {
			latest_imu.sample = imu_tmp;
			latest_imu.fresh = true;
		}

		adxl375_sample_t adxl_tmp;
		if (adxl375_poll_sample(&adxl_tmp) == ADXL375_POLL_OK) {
			latest_adxl.sample = adxl_tmp;
			latest_adxl.fresh = true;
		}

		ms5611_sample_t baro_tmp;
		if (ms5611_poll_sample(&baro_tmp) == MS5611_POLL_OK) {
			latest_baro.sample = baro_tmp;
			latest_baro.fresh = true;
		}

		uint16_t bat_tmp;
		if (adc_bat_lvl_poll(&bat_tmp) == BAT_LVL_POLL_OK) {
			latest_battery.sample_mv = bat_tmp;
			latest_battery.fresh = true;
		}

		// gnss_sample_t gnss_tmp;
		// if (max_m10s_poll_sample(&gnss_tmp) == MAX_M10S_POLL_OK) {
		// 	latest_gnss.sample = gnss_tmp;
		// 	latest_gnss.fresh = true;
		// }

		// if time elapsed, create and push the frame
		if ((int64_t)(now - next_frame_us) >= 0) {
			next_frame_us += FRAME_PERIOD_US;

			sensor_frame_t frame = {0};

			frame.sync_word = 0xA55A;
			frame.frame_number = frame_number++;
			frame.timestamp_us = now;

			frame.imu = latest_imu.sample;

			frame.adxl = latest_adxl.sample;

			frame.baro = latest_baro.sample;

			// frame.gnss = latest_gnss.sample;

			frame.battery_mv = latest_battery.sample_mv;

			if (latest_imu.fresh) {
				frame.freshness |= FRAME_IMU_FRESH;
			}

			if (latest_adxl.fresh) {
				frame.freshness |= FRAME_ADXL_FRESH;
			}

			if (latest_baro.fresh) {
				frame.freshness |= FRAME_BARO_FRESH;
			}

			// if (latest_gnss.fresh) {
			// 	frame.freshness |= FRAME_GNSS_FRESH;
			// }

			latest_imu.fresh = false; 
			latest_adxl.fresh = false;
			latest_baro.fresh = false;
			latest_battery.fresh = false;
			// latest_gnss.fresh = false;

			frame_ring_push(&frame_rb, &frame);
		}

		tight_loop_contents();
	}
}

void core1_entry(void) 
{
	sensor_frame_t frame;

	for EVER {
		if (frame_ring_pop(&frame_rb, &frame)) {
			frame.crc16 = crc16_ccitt_false(&frame);

			serial_debug_print(&frame);
			log_frame_to_sd(&frame);
			xbee_transmit(&frame, sizeof(frame));
		}
		else {
			tight_loop_contents();
		}
	}
}

void error_handler(void) 
{
	gpio_put(BLUE_LED, 0);
	gpio_put(RED_LED, 1);
	for EVER {
		sleep_ms(1000);
		printf("Error loop");
	}
}

void serial_debug_print(sensor_frame_t *frame) 
{
	printf(
		"\r[%llu us] "
		"IMU%s | "
		"gx: %.2f gy: %.2f gz: %.2f dps | "
		"ax: %.2f ay: %.2f az: %.2f g || "
		"ADXL%s | "
		"ax: %.2f ay: %.2f az: %.2f g || "
		"BARO%s | "
		"P: %.2f mbar T: %.2f C Alt: %.2f m     ",

		(unsigned long long)frame->timestamp_us,

		(frame->freshness & FRAME_IMU_FRESH) ? "*" : "",

		frame->imu.gyro_x_dps,
		frame->imu.gyro_y_dps,
		frame->imu.gyro_z_dps,

		frame->imu.accel_x_g,
		frame->imu.accel_y_g,
		frame->imu.accel_z_g,

		(frame->freshness & FRAME_ADXL_FRESH) ? "*" : "",

		frame->adxl.x_g,
		frame->adxl.y_g,
		frame->adxl.z_g,

		(frame->freshness & FRAME_BARO_FRESH) ? "*" : "",

		frame->baro.pressure_mbar,
		frame->baro.temperature_c,
		frame->baro.altitude_m
	);

	fflush(stdout);
}

void log_frame_to_sd(sensor_frame_t *frame)
{
	if (!sd_logger_append_frame_csv(frame)) {
		printf("\nSD frame log failed\n");
		fflush(stdout);
	}
}

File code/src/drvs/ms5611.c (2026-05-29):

#include "drvs/ms5611.h"

#include <math.h>
#include <string.h>

#include "pico/stdlib.h"
#include "hardware/i2c.h"

#define MS5611_CMD_ADC_READ      0x00
#define MS5611_CMD_RESET         0x1E
#define MS5611_CMD_CONVERT_D1    0x40
#define MS5611_CMD_CONVERT_D2    0x50
#define MS5611_CMD_PROM_READ     0xA0

typedef enum {
	MS5611_OK = 0,
	MS5611_ERR_I2C = -1,
	MS5611_ERR_PROM_CRC = -2,
	MS5611_ERR_BAD_PARAM = -3,
	MS5611_ERR_NOT_READY = -4
} ms5611_status_t;

enum {
	MS5611_STATE_START_D1 = 0,
	MS5611_STATE_WAIT_D1,
	MS5611_STATE_START_D2,
	MS5611_STATE_WAIT_D2
};

typedef struct {
	i2c_inst_t *i2c;
	uint8_t addr;

	uint16_t prom[8];

	uint32_t d1_raw;
	uint32_t d2_raw;

	int32_t temperature_centi_c;
	int32_t pressure_centi_mbar;

	ms5611_osr_t osr;

	bool sample_ready;

	uint8_t state;
	absolute_time_t conversion_deadline;

	bool calibrated;
	float ground_pressure_mbar;
} ms5611_dev_t;

static const uint32_t osr_delay_us[] = {
	600,    // OSR 256, datasheet max about 0.60 ms
	1170,   // OSR 512
	2280,   // OSR 1024
	4540,   // OSR 2048
	9040    // OSR 4096
};

static ms5611_dev_t g_ms5611;

static uint8_t osr_to_cmd_bits(ms5611_osr_t osr)
{
	return ((uint8_t)osr) * 2;
}

static ms5611_status_t write_cmd(ms5611_dev_t *dev, uint8_t cmd)
{
	int ret = i2c_write_timeout_us(
		dev->i2c,
		dev->addr,
		&cmd,
		1,
		false,
		MS5611_I2C_TIMEOUT_US
	);

	return ret == 1 ? MS5611_OK : MS5611_ERR_I2C;
}

static ms5611_status_t read_prom_word(ms5611_dev_t *dev, uint8_t index, uint16_t *out)
{
	uint8_t cmd = MS5611_CMD_PROM_READ + (index * 2);
	uint8_t buf[2];

	int ret = i2c_write_timeout_us(
		dev->i2c,
		dev->addr,
		&cmd,
		1,
		true,
		MS5611_I2C_TIMEOUT_US
	);
	if (ret != 1) {
		return MS5611_ERR_I2C;
	}

	ret = i2c_read_timeout_us(
		dev->i2c,
		dev->addr,
		buf,
		2,
		false,
		MS5611_I2C_TIMEOUT_US
	);
	if (ret != 2) {
		return MS5611_ERR_I2C;
	}

	*out = ((uint16_t)buf[0] << 8) | buf[1];
	return MS5611_OK;
}

static ms5611_status_t read_adc(ms5611_dev_t *dev, uint32_t *out)
{
	uint8_t cmd = MS5611_CMD_ADC_READ;
	uint8_t buf[3];

	int ret = i2c_write_timeout_us(
		dev->i2c,
		dev->addr,
		&cmd,
		1,
		true,
		MS5611_I2C_TIMEOUT_US
	);
	if (ret != 1) {
		return MS5611_ERR_I2C;
	}

	ret = i2c_read_timeout_us(
		dev->i2c,
		dev->addr,
		buf,
		3,
		false,
		MS5611_I2C_TIMEOUT_US
	);
	if (ret != 3) {
		return MS5611_ERR_I2C;
	}

	*out = ((uint32_t)buf[0] << 16) |
		((uint32_t)buf[1] << 8)  |
		((uint32_t)buf[2]);

	return MS5611_OK;
}

/*
 * CRC-4 check from MS5611 datasheet/application-note style algorithm.
 * prom[7] low nibble contains the stored CRC.
 */
static uint8_t crc4(uint16_t prom[8])
{
	uint16_t n_rem = 0;
	uint16_t crc_read = prom[7] & 0x000F;

	prom[7] &= 0xFF00;

	for (uint8_t cnt = 0; cnt < 16; cnt++) {
		if (cnt & 1) {
			n_rem ^= prom[cnt >> 1] & 0x00FF;
		} else {
			n_rem ^= prom[cnt >> 1] >> 8;
		}

		for (uint8_t bit = 0; bit < 8; bit++) {
			if (n_rem & 0x8000) {
				n_rem = (n_rem << 1) ^ 0x3000;
			} else {
				n_rem <<= 1;
			}
		}
	}

	prom[7] |= crc_read;
	return (n_rem >> 12) & 0x000F;
}

static void compensate(ms5611_dev_t *dev)
{
	const int64_t C1 = dev->prom[1];
	const int64_t C2 = dev->prom[2];
	const int64_t C3 = dev->prom[3];
	const int64_t C4 = dev->prom[4];
	const int64_t C5 = dev->prom[5];
	const int64_t C6 = dev->prom[6];

	int64_t D1 = dev->d1_raw;
	int64_t D2 = dev->d2_raw;

	int64_t dT = D2 - (C5 << 8);
	int64_t TEMP = 2000 + ((dT * C6) >> 23);

	int64_t OFF  = (C2 << 16) + ((C4 * dT) >> 7);
	int64_t SENS = (C1 << 15) + ((C3 * dT) >> 8);

	/*
     * Second-order temperature compensation.
     * Important below 20°C, especially below -15°C.
     */
	int64_t T2 = 0;
	int64_t OFF2 = 0;
	int64_t SENS2 = 0;

	if (TEMP < 2000) {
		int64_t t = TEMP - 2000;
		T2 = (dT * dT) >> 31;
		OFF2 = (5 * t * t) >> 1;
		SENS2 = (5 * t * t) >> 2;

		if (TEMP < -1500) {
			int64_t t2 = TEMP + 1500;
			OFF2 += 7 * t2 * t2;
			SENS2 += (11 * t2 * t2) >> 1;
		}
	} else {
		int64_t t = TEMP - 2000;
		T2 = 0;
		OFF2 = 0;
		SENS2 = (5 * t * t) >> 3;
	}

	TEMP -= T2;
	OFF -= OFF2;
	SENS -= SENS2;

	int64_t P = (((D1 * SENS) >> 21) - OFF) >> 15;

	dev->temperature_centi_c = (int32_t)TEMP;
	dev->pressure_centi_mbar = (int32_t)P;
}

static ms5611_status_t init_device(ms5611_dev_t *dev, i2c_inst_t *i2c, uint8_t addr,
				   ms5611_osr_t osr)
{
	if (!dev || !i2c || osr > MS5611_OSR_4096) {
		return MS5611_ERR_BAD_PARAM;
	}

	memset(dev, 0, sizeof(*dev));

	dev->i2c = i2c;
	dev->addr = addr;
	dev->osr = osr;
	dev->state = MS5611_STATE_START_D1;

	ms5611_status_t st = write_cmd(dev, MS5611_CMD_RESET);
	if (st != MS5611_OK) {
		return st;
	}

	/*
     * Reset reload time is around 2.8 ms according to datasheet.
     * This is inside init only, so blocking here is usually acceptable.
     */
	sleep_ms(3);

	for (uint8_t i = 0; i < 8; i++) {
		st = read_prom_word(dev, i, &dev->prom[i]);
		if (st != MS5611_OK) {
			return st;
		}
	}

	uint16_t prom_copy[8];
	memcpy(prom_copy, dev->prom, sizeof(prom_copy));

	uint8_t crc_calc = crc4(prom_copy);
	uint8_t crc_stored = dev->prom[7] & 0x000F;

	if (crc_calc != crc_stored) {
		return MS5611_ERR_PROM_CRC;
	}

	return MS5611_OK;
}

static ms5611_status_t poll_device(ms5611_dev_t *dev)
{
	if (!dev) {
		return MS5611_ERR_BAD_PARAM;
	}

	ms5611_status_t st;

	switch (dev->state) {
		case MS5611_STATE_START_D1: {
			uint8_t cmd = MS5611_CMD_CONVERT_D1 + osr_to_cmd_bits(dev->osr);
			st = write_cmd(dev, cmd);
			if (st != MS5611_OK) {
				return st;
			}

			dev->conversion_deadline = make_timeout_time_us(osr_delay_us[dev->osr]);
			dev->state = MS5611_STATE_WAIT_D1;
			return MS5611_OK;
		}

		case MS5611_STATE_WAIT_D1:
			if (!time_reached(dev->conversion_deadline)) {
				return MS5611_ERR_NOT_READY;
			}

			st = read_adc(dev, &dev->d1_raw);
			if (st != MS5611_OK) {
				return st;
			}

			dev->state = MS5611_STATE_START_D2;
			return MS5611_OK;

		case MS5611_STATE_START_D2: {
			uint8_t cmd = MS5611_CMD_CONVERT_D2 + osr_to_cmd_bits(dev->osr);
			st = write_cmd(dev, cmd);
			if (st != MS5611_OK) {
				return st;
			}

			dev->conversion_deadline = make_timeout_time_us(osr_delay_us[dev->osr]);
			dev->state = MS5611_STATE_WAIT_D2;
			return MS5611_OK;
		}

		case MS5611_STATE_WAIT_D2:
			if (!time_reached(dev->conversion_deadline)) {
				return MS5611_ERR_NOT_READY;
			}

			st = read_adc(dev, &dev->d2_raw);
			if (st != MS5611_OK) {
				return st;
			}

			compensate(dev);
			dev->sample_ready = true;

			dev->state = MS5611_STATE_START_D1;
			return MS5611_OK;

		default:
			dev->state = MS5611_STATE_START_D1;
			return MS5611_ERR_BAD_PARAM;
	}
}

static bool sample_ready(const ms5611_dev_t *dev)
{
	return dev && dev->sample_ready;
}

static void clear_sample_ready(ms5611_dev_t *dev)
{
	if (dev) {
		dev->sample_ready = false;
	}
}

static float get_pressure_mbar(const ms5611_dev_t *dev)
{
	return dev ? dev->pressure_centi_mbar / 100.0f : 0.0f;
}
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

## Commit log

2025-10-07 first commit :^D
    [flight_comp_srad-2026.kicad_pcb, flight_comp_srad-2026.kicad_sch]
2025-10-13 agregue datasheets y puse pines para el xbee
    [MOD18_MAX-M10M_UBL.step, flight_comp_srad-2026.kicad_pcb, flight_comp_srad-2026.kicad_sch]
2025-10-27 added new imu's
    [flight_comp_srad-2026.kicad_pcb, flight_comp_srad-2026.kicad_sch]
2025-10-27 added adx 3d model
    [ADXL375BCCZ-RL7.STEP, flight_comp_srad-2026.kicad_pcb]
2025-10-27 added xtal
    [flight_comp_srad-2026.kicad_pcb, flight_comp_srad-2026.kicad_sch]
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2025-11-03 mas cosas al schem
    [RP2040_QFN_PACKAGE.STEP, flight_comp_srad-2026.kicad_pcb, flight_comp_srad-2026.kicad_sch]
2025-11-20 nuevos componentes menos xtal
    [flight_comp_srad-2026.kicad_pcb]
2025-11-20 xtal smd
    [flight_comp_srad-2026.kicad_pcb, flight_comp_srad-2026.kicad_sch]
2025-12-04 agregue xbee footprint, symb y .step
    [XBP9B-DMSTB002.step, flight_comp_srad-2026.kicad_pcb, flight_comp_srad-2026.kicad_sch]
2025-12-05 todos los IC menos XBEE
    [503398-1892.step, ABM8-272-T3.step, IIM-20670.step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]
2025-12-05 schematic del rp2040 hecho
    [flight_comp_srad-2026.kicad_pcb]
2025-12-06 RP2040 listo, faltan sensores y comms
    [flight_comp_srad-2026.kicad_pcb, flight_comp_srad-2026.kicad_sch, sensors.kicad_sch]
2025-12-06 cosas del xbee
    [flight_comp_srad-2026.kicad_pcb, flight_comp_srad-2026.kicad_sch]
2025-12-07 footprints y cosas
    [503398-1892--3DModel-STEP-56544.STEP, IIM-20670--3DModel-STEP-269445.STEP, MS561101BA03-50--3DModel-STEP-56544.STEP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]
2025-12-09 queda cablear los gpios
    [ABM8-272-T3.STEP, PTS810SJK250SMTR_LFS.step, flight_comp_srad-2026.kicad_pcb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]
2025-12-10 plano de masa y antena puestos
    [flight_comp_srad-2026.kicad_pcb, flight_comp_srad-2026.kicad_sch]
2025-12-14 conectado spi del iim y ruteo de algunos caps de desacople
    [flight_comp_srad-2026.kicad_pcb, flight_comp_srad-2026.kicad_sch]
2025-12-17 listo los caps de desacople de la rp2040
    [flight_comp_srad-2026.kicad_pcb, flight_comp_srad-2026.kicad_sch]
2025-12-17 listo el routeo de casi todo falta layer gnd y 3v3, capas adxl
    [flight_comp_srad-2026.kicad_pcb, flight_comp_srad-2026.kicad_sch]
2025-12-26 Planos de 3V3 y VBUS, y otras cositas
    Planos de 3V3 y VBUS, y otras cositas
    [flight_comp_srad-2026.kicad_pcb, flight_comp_srad-2026.kicad_sch]
2025-12-29 2 LEDs are back, ruteo pistas SD y pistas bananeras de 3V3 y GND
    [flight_comp_srad-2026.kicad_pcb, flight_comp_srad-2026.kicad_sch]
2026-01-02 Pistas terminadas (FALTA REVISAR) + medidor tensión batería
    [flight_comp_srad-2026.kicad_pcb, flight_comp_srad-2026.kicad_sch]
2026-01-02 Pistas terminadas (FALTA REVISAR) + medidor tensión batería
    Me faltó poner una pista más xd
    [flight_comp_srad-2026.kicad_pcb]
2026-01-04 routeo listo, falta revisar las conecc
    [flight_comp_srad-2026.kicad_pcb, flight_comp_srad-2026.kicad_sch]
2026-01-04 agregue coments
    [flight_comp_srad-2026.kicad_pcb, flight_comp_srad-2026.kicad_sch]
2026-01-07 Cambio plano 3v3
    [flight_comp_srad-2026.kicad_pcb]
2026-01-12 linea de transmision ruteada
    [flight_comp_srad-2026-B_Cu.gbr, flight_comp_srad-2026-B_Mask.gbr, flight_comp_srad-2026-B_Paste.gbr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]
2026-02-01 Update flight_comp_srad-2026.kicad_pcb
    1ra versión serigrafía
    [flight_comp_srad-2026.kicad_pcb]
2026-02-04 Cambio de regulador de tensión - chequear impedancia de línea
    [TPS73733DCQ.step, flight_comp_srad-2026.kicad_pcb]
2026-02-04 SCHK de lo anterior - cambio en reg de tension
    me olvide de guardar el esquematico antes de pushear lo anterior
    [flight_comp_srad-2026.kicad_sch]
2026-02-10 Realimentación bien hecha y agujeros ajustados
    [flight_comp_srad-2026.kicad_pcb, flight_comp_srad-2026.kicad_sch]
2026-02-10 Final?
    Can you beat KiCAD with dementia?
    [flight_comp_srad-2026-B_Cu.gbr, flight_comp_srad-2026-B_Mask.gbr, flight_comp_srad-2026-B_Paste.gbr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]
2026-02-10 cambio P-UPs y BOOT a 0805
    [flight_comp_srad-2026.kicad_pcb, flight_comp_srad-2026.kicad_sch]
2026-02-10 agregue beeper que falta conectar, saque vias abajo de pads y saque la filling zone gnd del bottom del regulador
    [PS1240P02BT.step, flight_comp_srad-2026.kicad_sch]
2026-02-10 beeper listo
    [flight_comp_srad-2026.kicad_pcb, flight_comp_srad-2026.kicad_sch]
2026-02-10 beeper listo listo
    [flight_comp_srad-2026.kicad_pcb, flight_comp_srad-2026.kicad_sch]
2026-02-18 quedan 62 errores de DRC mas warnings
    principales errores:
    - clearance violation (no sé por qué está en 0.2mm pero no puedo cambiarlo XD)
    - cortos por las vias más grandes
    - boludeces de la serigrafía, habría que volar todo lo que no sea importante
    - falta poner shunt a la linea de tx, no se como porque no entra XD
    - más boludeces como la posición del USB, está bien que sobresalga (ver capa user drawings) pero da error
    [flight_comp_srad-2026-B_Cu.gbr, flight_comp_srad-2026-B_Mask.gbr, flight_comp_srad-2026-B_Paste.gbr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]
2026-02-18 Adición buzzer y corrección de algunos errores
    [flight_comp_srad-2026.kicad_pcb, flight_comp_srad-2026.kicad_sch]
2026-02-19 quedan 5 errores
    creo que todos los errores son inevitables por el diseño. quedan cosas tipo ancho del texto, pero debería salir bien todo lo importante en JLC
    [flight_comp_srad-2026.kicad_pcb, flight_comp_srad-2026.kicad_sch]
2026-02-22 srad versión final ahora sí 2.0 intento 17
    nigga
    [flight_comp_srad-2026.kicad_pcb, flight_comp_srad-2026.kicad_sch]
2026-04-11 PARECE terminado
    [Required_impedance_control.xlsx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]
2026-04-11 version final?
    uwu
    [flight_comp_srad-2026.kicad_pcb, flight_comp_srad-2026.kicad_sch]
2026-04-11 versión final ahora sí
    OwO
    [flight_comp_srad-2026.kicad_pcb, flight_comp_srad-2026.kicad_sch]
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2026-05-06 cleaned unused kicad dirs and files
    [503398-1892.step, ABM8-272-T3.step, IIM-20670.step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]
2026-05-07 testing iim drv, not working for now
    [iim20670.c, iim20670.h, main.c]
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2026-05-17 cleaner APIs for sensors. also noticed pressure readings have little drift
    [adxl375.c, adxl375.h, iim20670.c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]
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2026-05-20 fixed bug on iim calibration
    [iim20670.c, iim20670.h, ms5611.h]
2026-05-20 used the error_handler in main
    [main.c]
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2026-05-29 corrected the telemetry_frame and added __attribute((packed))__ to every sensor struct
    [adxl375.h, iim20670.h, ms5611.h]
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2026-05-29 added buzzer at the start
    [main.c]
2026-05-29 changed directories for /include/drvs
    [flight_comp_srad-2026.kicad_sch]
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2026-06-05 bug fix in adxl calibration
    [adxl375.c, adxl375.h, main.c]
